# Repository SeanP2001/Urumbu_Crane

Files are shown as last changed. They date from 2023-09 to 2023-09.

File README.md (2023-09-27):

# Urumbu Crane

## Table of Contents <!-- omit from toc -->

- [Introduction](#introduction)
- [Design](#design)
  - [Y-Axis Drum](#y-axis-drum)
  - [X-Axis Drive Section](#x-axis-drive-section)
  - [X-Axis Carriage](#x-axis-carriage)
  - [Tail Pulley](#tail-pulley)
  - [Hook](#hook)
  - [End Plates](#end-plates)
  - [Frame](#frame)
- [Manufacturing](#manufacturing)
  - [3D Printing](#3d-printing)
  - [CNC Routing](#cnc-routing)
  - [Laser Cutting](#laser-cutting)
  - [Assembling](#assembling)
- [Software](#software)
- [Build Video and Demonstration](#build-video-and-demonstration)
- [Conclusion](#conclusion)

## Introduction

I designed a set of Urumbu USB stepper motor modules for students in the FabLAB to use for rapidly prototype motion systems. The files to create these modules can be found in my ["Urumbu_USB_Stepper_Motor" repostiory](https://github.com/SeanP2001/Urumbu_USB_Stepper_Motor). 

I designed and built this crane to test and demonstrate the use of the modules. This repository serves as documentation of a project which students can reference when learning how to use the modules.

## Design

<p align="center">
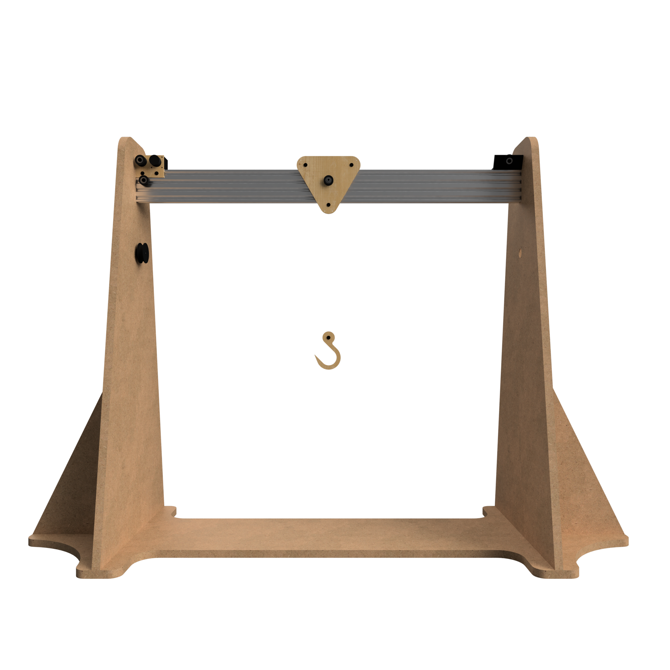
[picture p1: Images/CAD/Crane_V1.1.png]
  
</p>

### Y-Axis Drum

<p align="center">
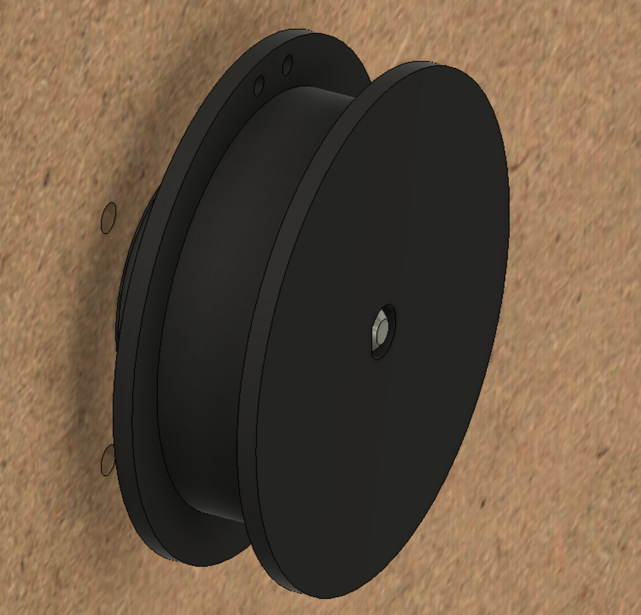
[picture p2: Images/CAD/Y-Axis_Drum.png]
   
</p>

Design Features:
- Two holes to tie the fishing line to.
- Reels in the fishing line.
- Friction fits onto NEMA 14 motor D-shaft.

### X-Axis Drive Section

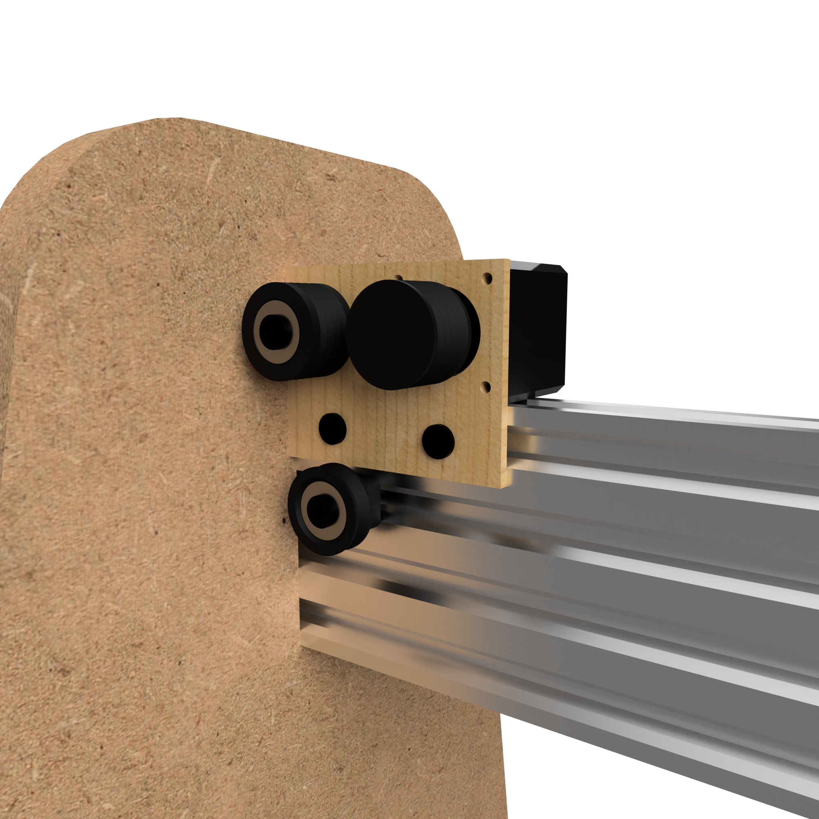
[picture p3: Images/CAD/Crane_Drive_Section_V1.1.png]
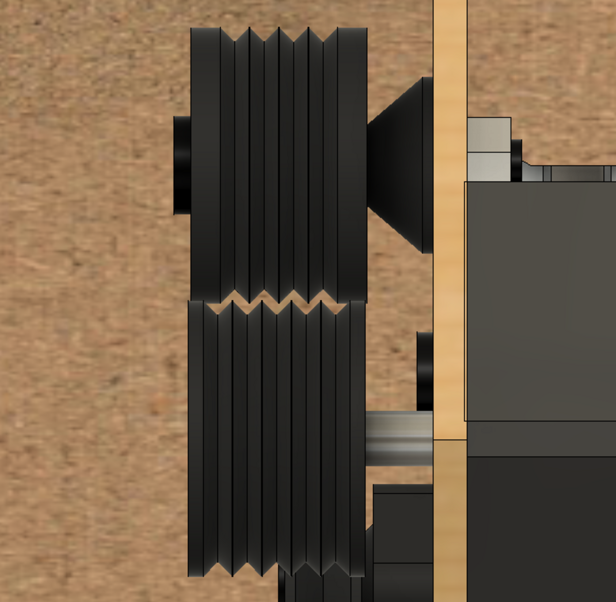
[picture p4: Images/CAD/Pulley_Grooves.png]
|   |  |
| --- | --- |

Design Features:
- Mounts the NEMA 14 motor to the aluminium extrusion.
- Secured to the aluminium extrusion using two M5 tee-nuts.
- Tensioner pulley increases friction between the motor pulley and fishing line, preventing it from slipping.
- Tensioner pulley has two bearings to help the fishing line move smoothly.

### X-Axis Carriage

<p align="center">
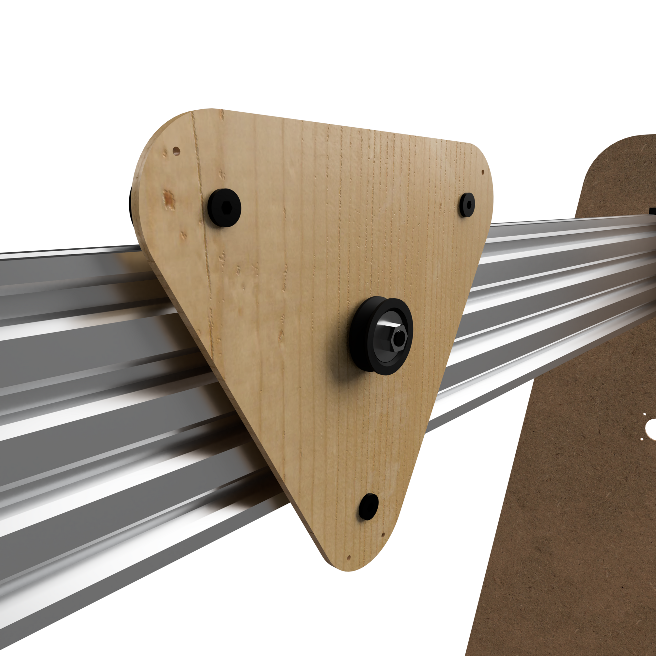
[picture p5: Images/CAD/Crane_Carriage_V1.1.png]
   
</p>

Design Features:
- Three M5 bolts secure spacers and Delrin V-wheels 
- The V-wheels slot into the V-slot linear rail, allowing the carriage to glide smoothly along the axis.
- Two holes for tying the x-axis fishing line to.
- A central pulley, to allow the fishing line to run over it and down to the hook.
- Two holes for the y-axis fishing line to be tied to after going through the hook. (There are two symmetrical holes to allow for the fishing line to come from the left or right side of the crane)

### Tail Pulley

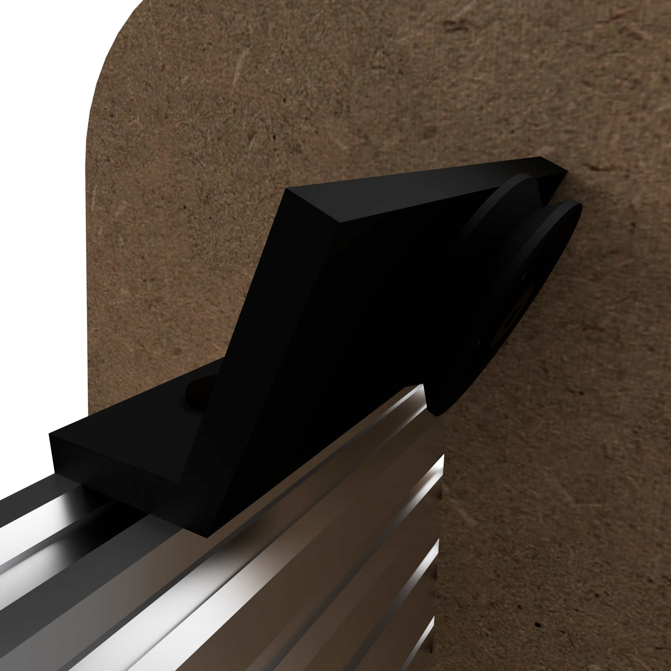
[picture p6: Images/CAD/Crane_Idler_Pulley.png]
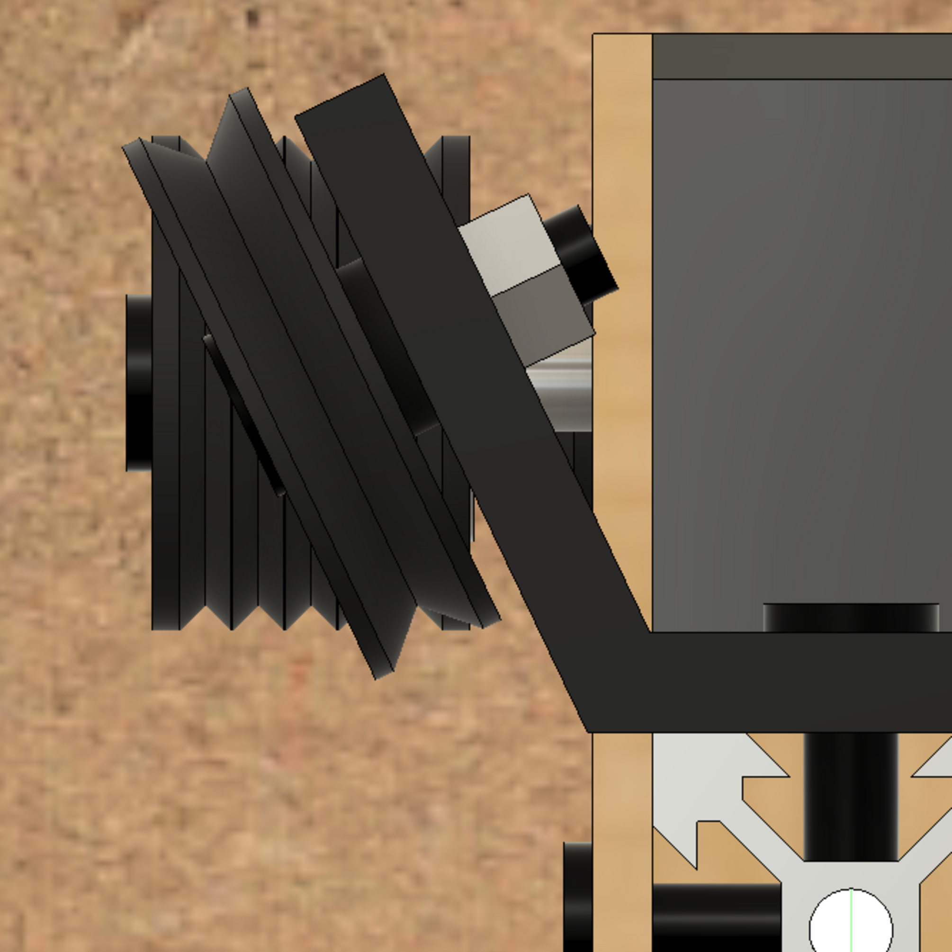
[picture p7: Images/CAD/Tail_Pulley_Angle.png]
|   |  |
| --- | --- |

Design Features:
- 3D printed bracket to secure the pulley to the aluminium extrusion at an angle. The angle matches the angle of the fishing line, allowing it to travel in a straight line from the motor pulley.
- Mounted to the extrusion with two M5 tee-nuts.

### Hook

<p align="center">
   
</p>

Design Features:
- Made from 5 layers of laser cut 3mm plywood glued together.
- Includes a pulley for the fishing line to go through and back up to the carriage. The doubled-up line prevents the hook from easily spinning.

### End Plates

<p align="center">
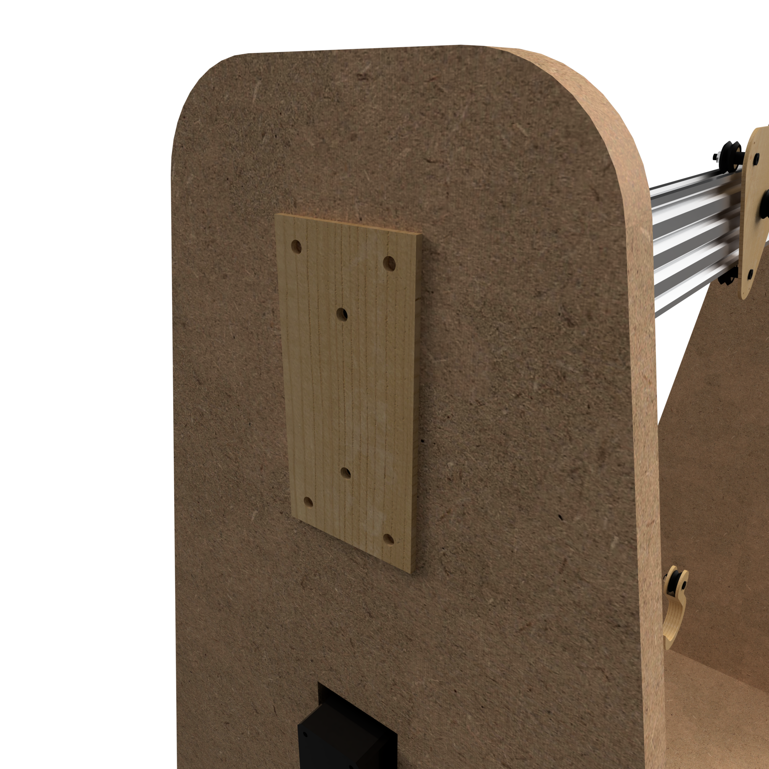
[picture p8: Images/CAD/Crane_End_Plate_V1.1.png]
   
</p>

Design Features:
- Two central holes to secure the plates to the tapped holes in the aluminium extrusion using M5 bolts.
- Four corner holes to secure the plates to the MDF frame with self-tapping wood screws.  

### Frame

<p align="center">
   
</p>

Design Features:
- Slot together with mortise and temon joints (dogboned to take into account the radius of the end mill)
- Symmetrical to allow the Y-axis motor to be mounted on either the left or right side.

## Manufacturing

### 3D Printing

I created a new Fusion360 file and imported the 3D printed bodies from the main Fusion360 file. I then laid out all of the parts flat on the XZ plane before exporting the STL file.

I opened the STL file in Cura and sliced the file for my 3D printer. I saved the Gcode to the microSD card to transfer the file to the printer.

<p align="center">
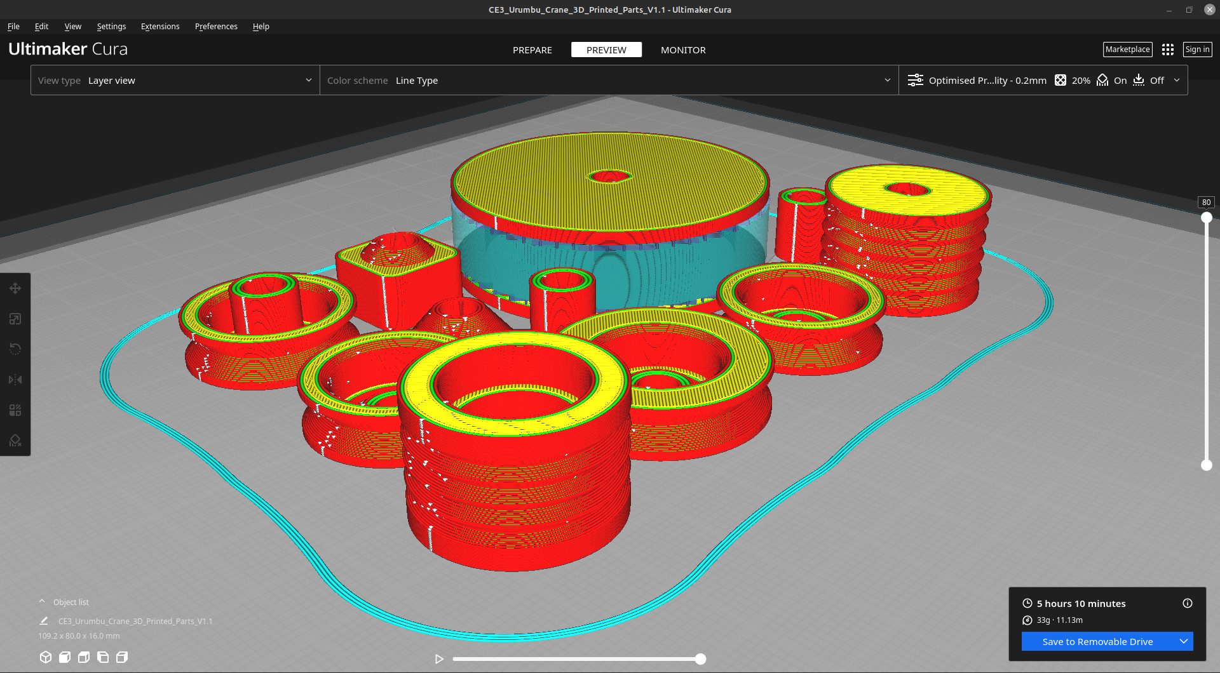
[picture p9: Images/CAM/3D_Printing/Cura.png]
  
</p>

I printed the parts using black PLA filament.

<p align="center">
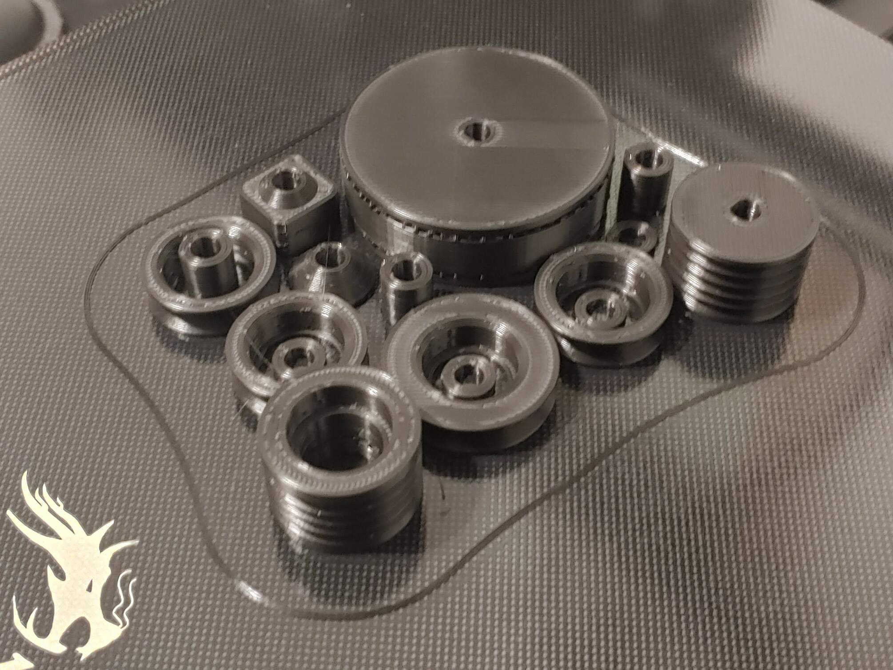
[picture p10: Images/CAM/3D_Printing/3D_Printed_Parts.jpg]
  
</p>

### CNC Routing

The MDF parts were imported into two new Fusion 360 designs, laid flat on the XZ plane and arranged to fit 8’x4’ sheets of MDF. Using the "Manufacturing" workspace, a new "Setup" was created, defining the type of CNC operation and the material properties. The "2D Pocket" and "2D Contour" operations were used to create the toolpaths.

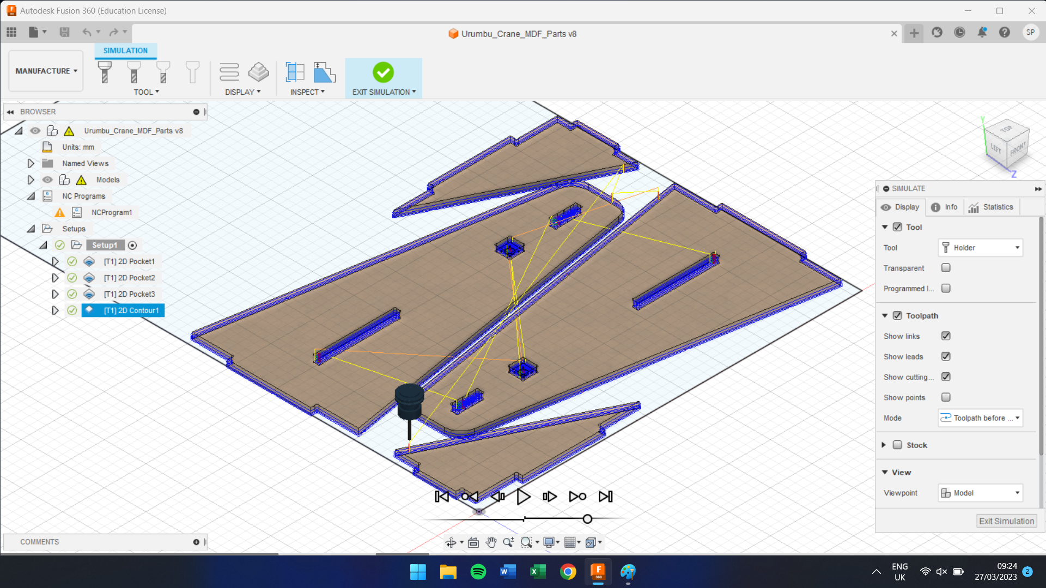
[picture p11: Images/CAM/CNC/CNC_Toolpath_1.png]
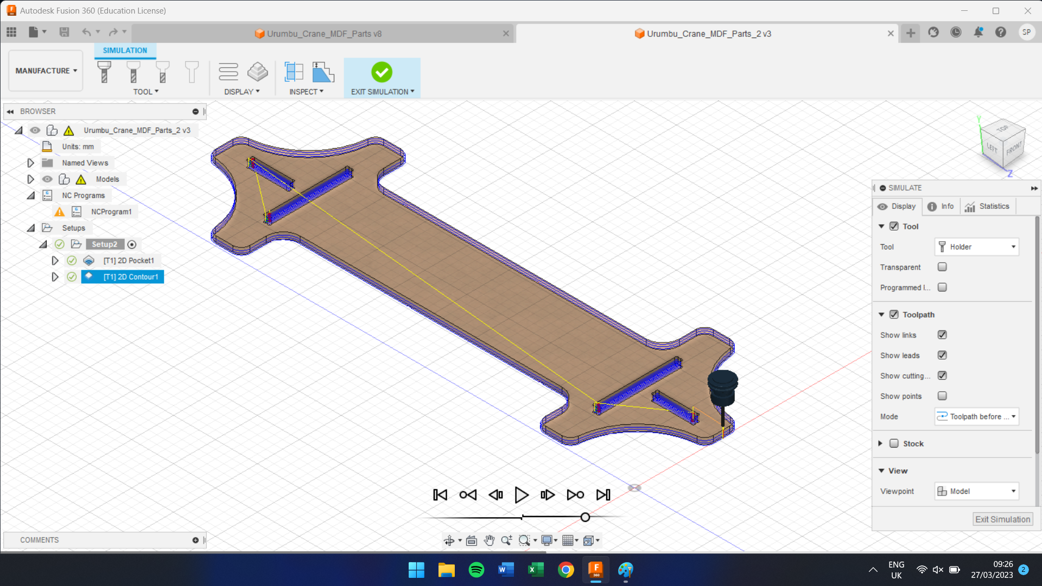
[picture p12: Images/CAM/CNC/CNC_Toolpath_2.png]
|   |  |
| --- | --- |

The toolpaths were exported as `.nc` files and saved to a USB stick. The USB stick was plugged into the large format CNC machine controller. The MDF was placed on the CNC, the vacuum table and extraction were turned on, the origins were set and the files were selected to cut.

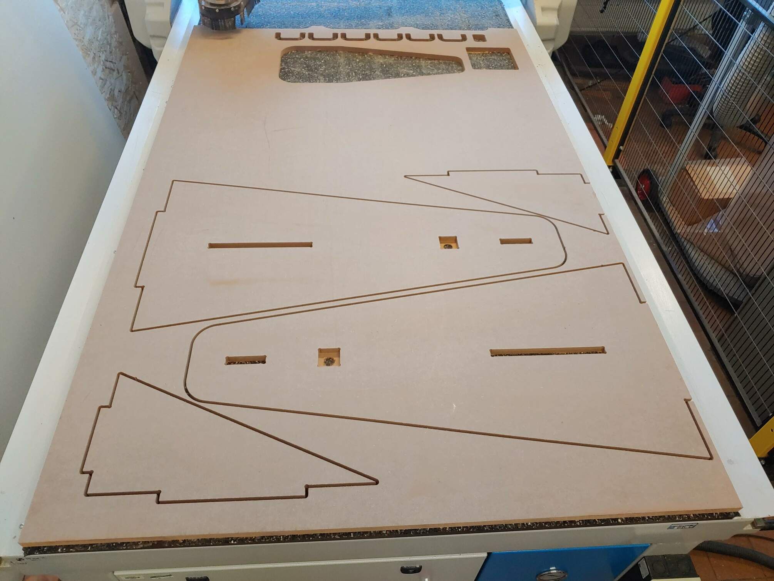
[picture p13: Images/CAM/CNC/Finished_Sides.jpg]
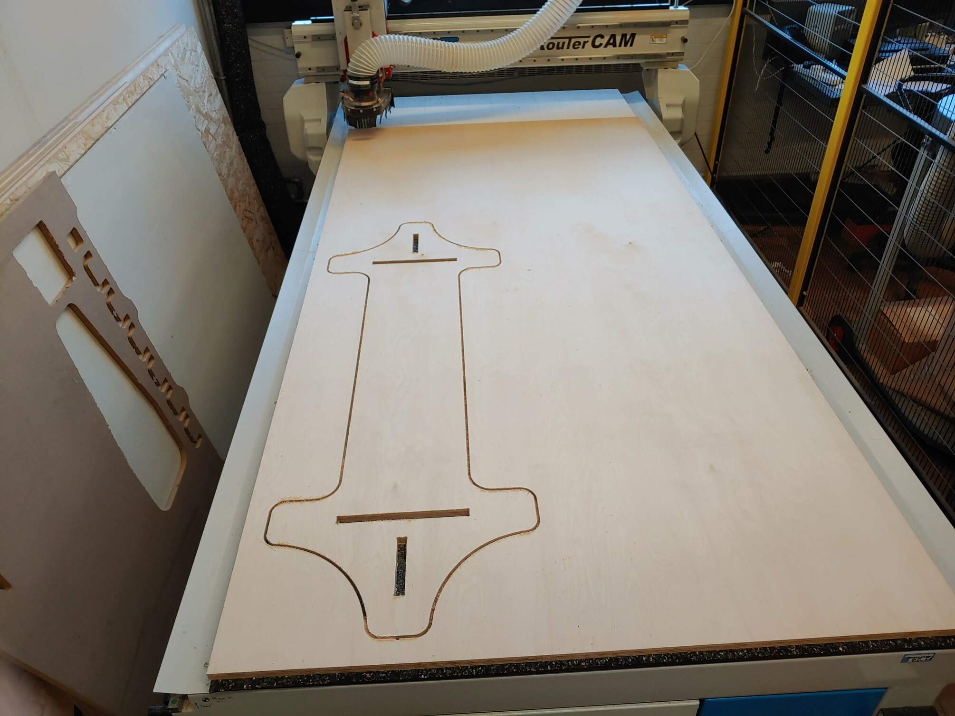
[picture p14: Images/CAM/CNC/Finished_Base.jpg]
|   |  |
| --- | --- |

### Laser Cutting

Using the Fusion 360 app "Shaper", I created SVG images for all the profiles that needed laser cutting.

<p align="center">
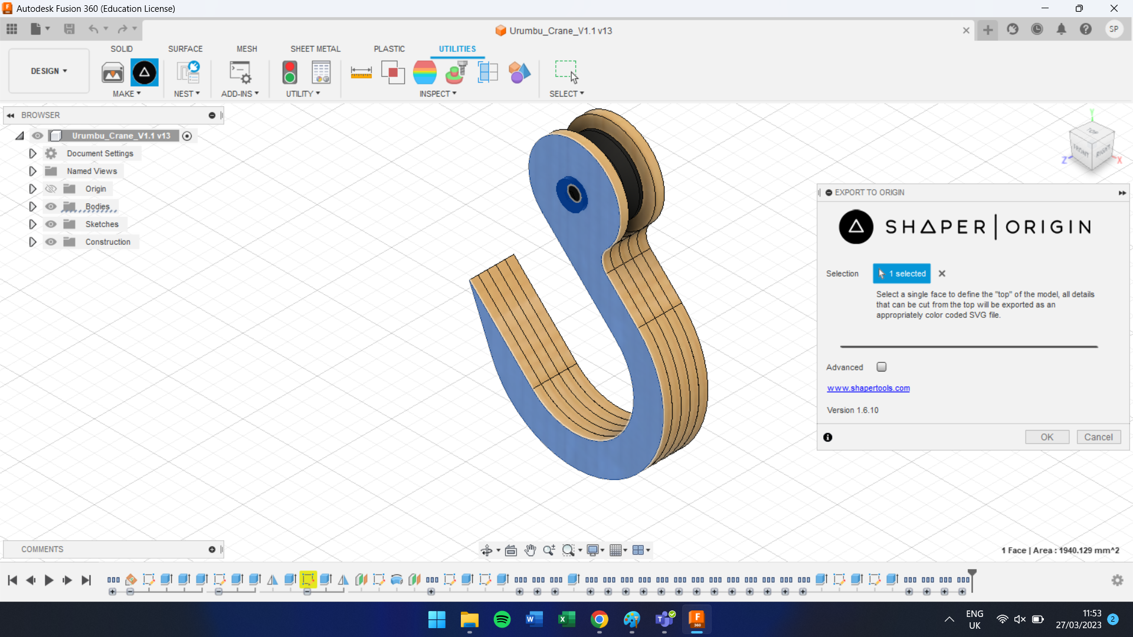
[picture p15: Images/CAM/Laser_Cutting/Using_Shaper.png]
  
</p>

This created SVG images of the end plate, carriage, outer hook, inner hook and motor mount profiles.

These profiles were imported into Inkscape and altered to have a red outline with no fill. The profiles were arranged to best use the space.

<p align="center">
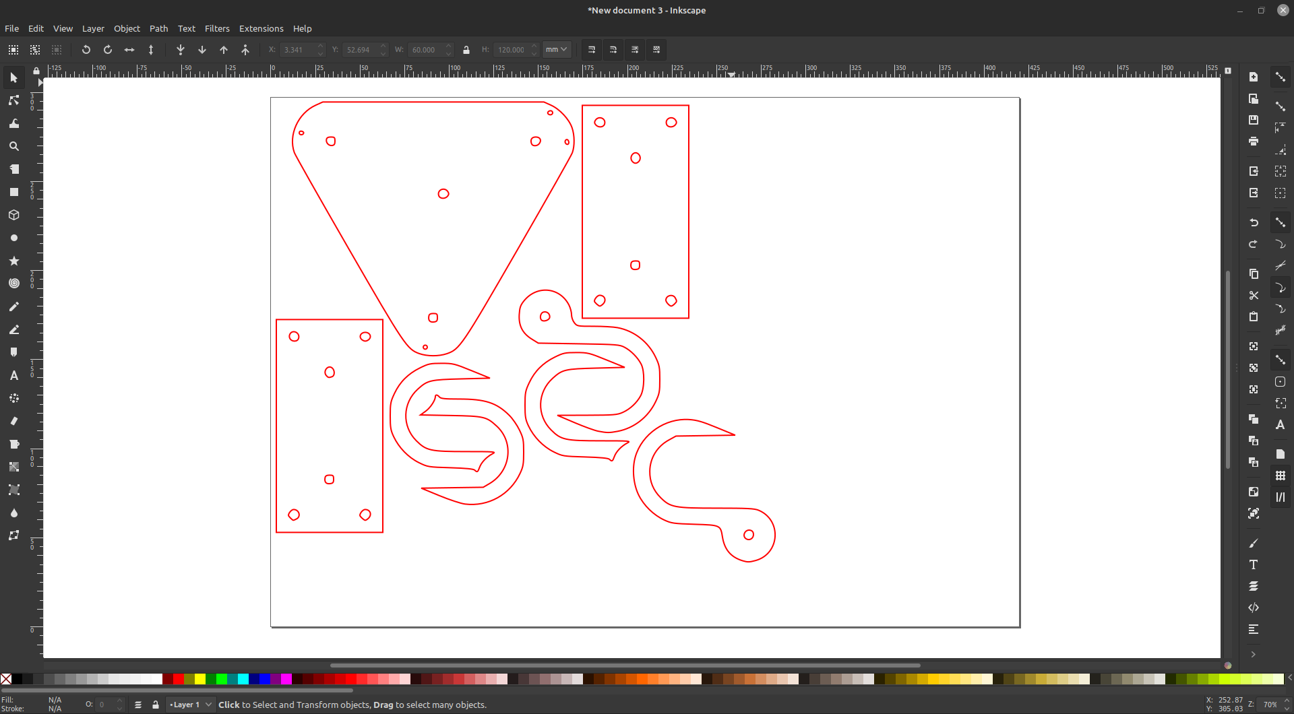
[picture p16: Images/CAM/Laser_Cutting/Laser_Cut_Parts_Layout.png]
  
</p>

In CorelDRAW, all lines were set to hairline thickness, and the file was sent to "print" on the Trotec Speedy400 laser-cutter. This opened Trotec JobControl. 

The 3mm Plywood was placed on the bed of the laser cutter, the laser height and position were set, and the lid was closed. In JobControl, the file was dragged to the position of the laser and set to cut.

<p align="center">
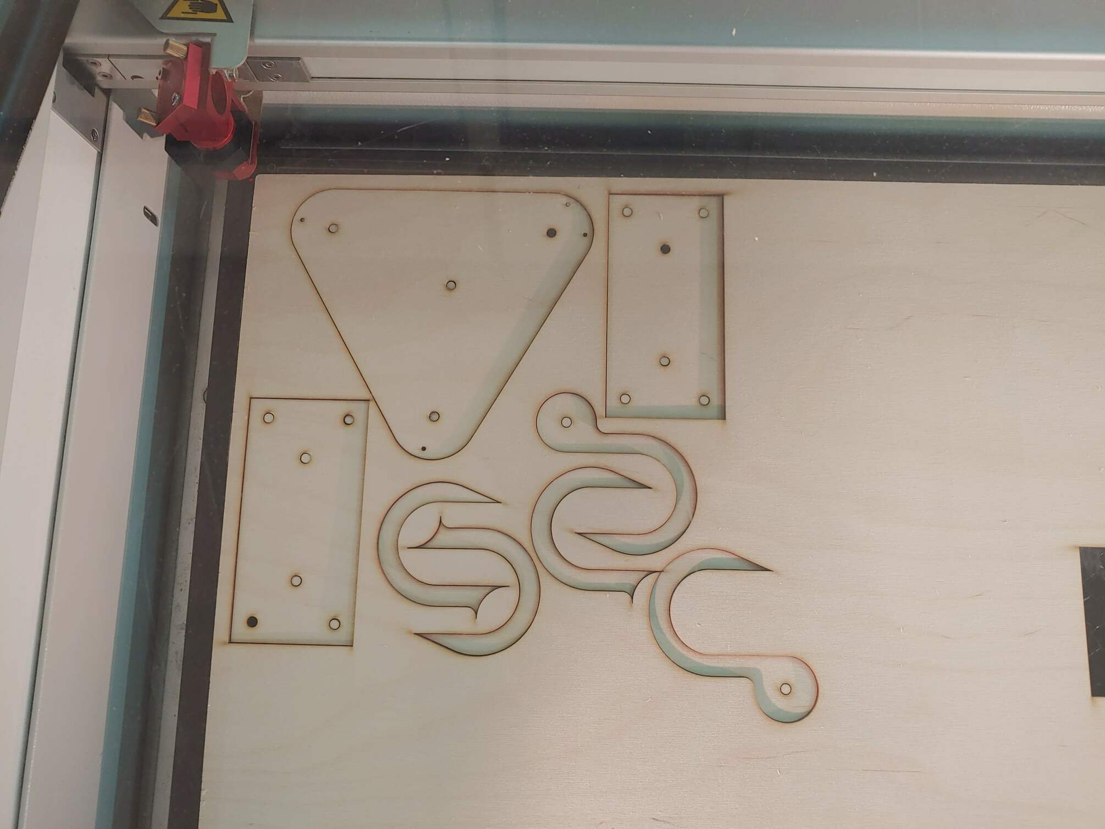
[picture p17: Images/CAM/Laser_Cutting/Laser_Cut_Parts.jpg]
  
</p>

### Assembling

- Slotted the frame together.
- Tapped M5 threads into 80x20x1000mm aluminium extrusion ends.
- Bolted the end plates to the ends of the aluminium extrusion.
- Screwed the end plates to the frame.

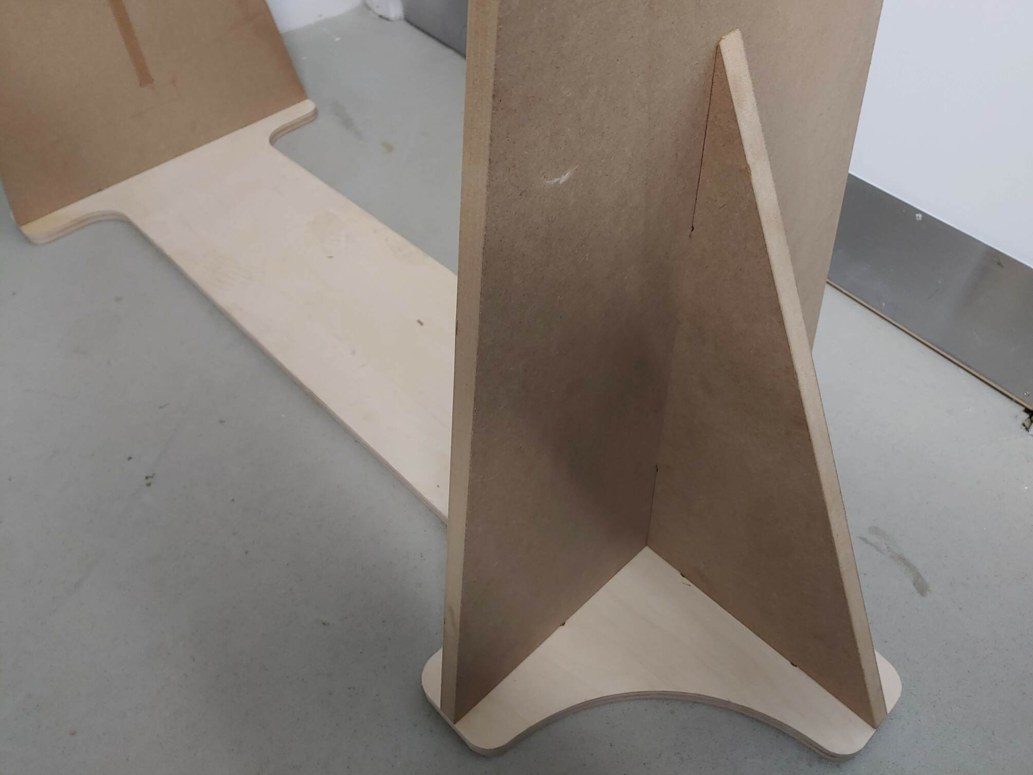
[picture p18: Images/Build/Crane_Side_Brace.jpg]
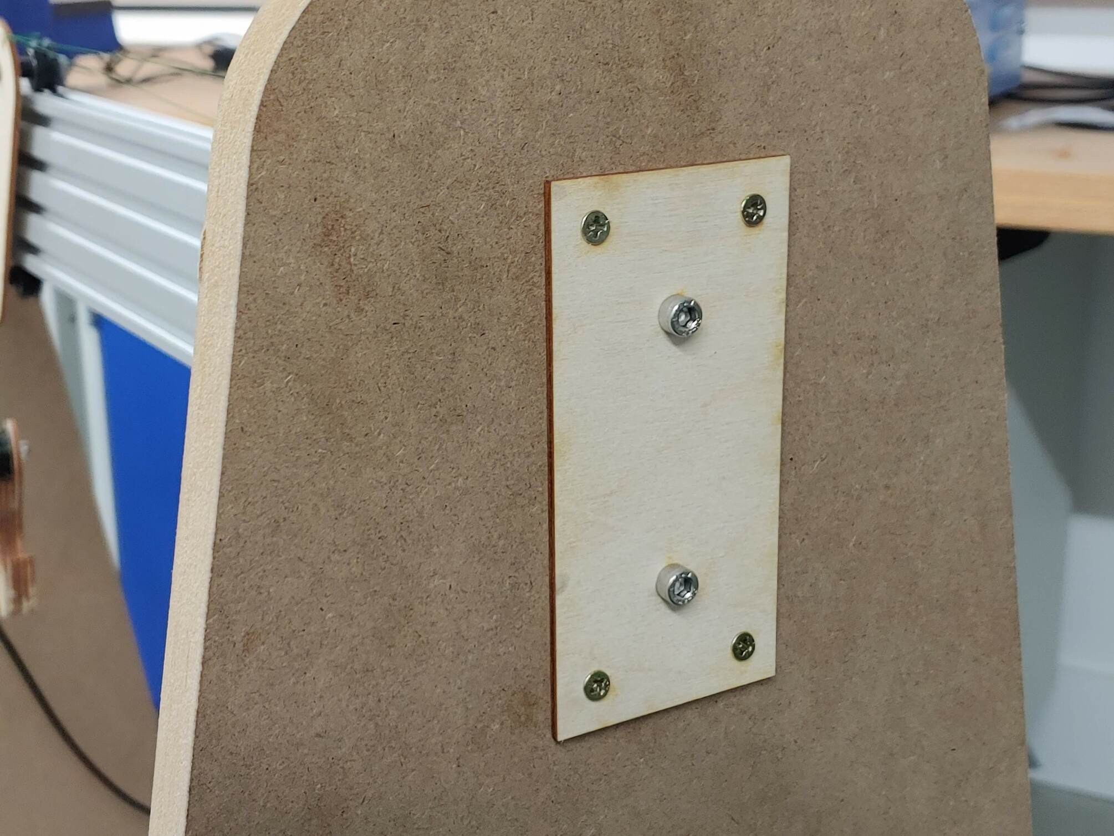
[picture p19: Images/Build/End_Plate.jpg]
|   |  |
| --- | --- |
  
- Glued the hook profiles together.
  
<p align="center">
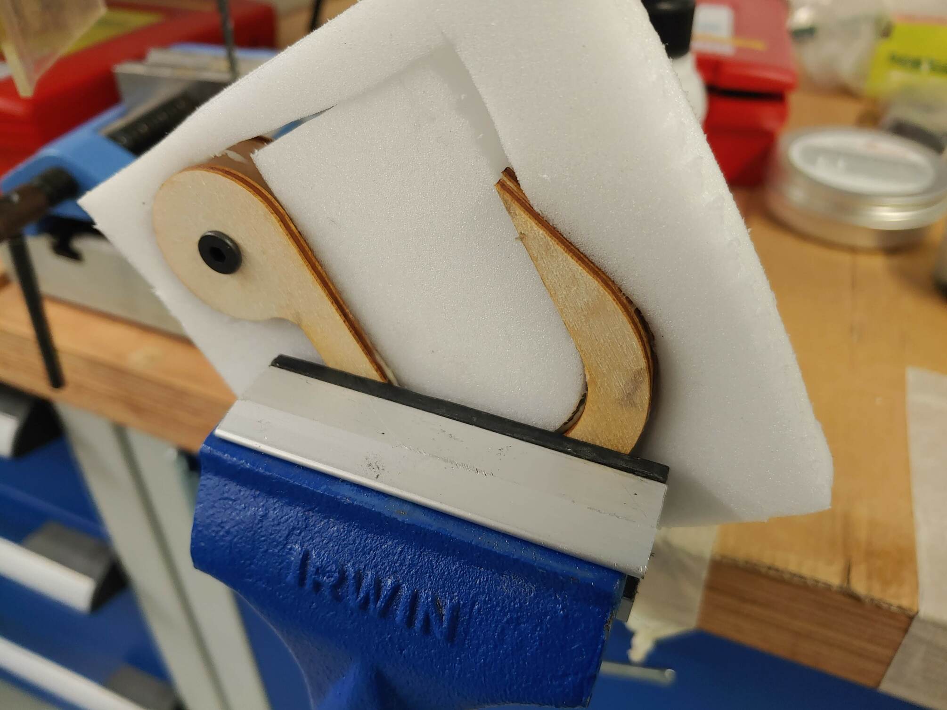
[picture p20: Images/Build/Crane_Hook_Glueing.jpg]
  
</p>

- Fixed both motors in place using M3 bolts.
- Covered the backs of both motors with electrical tape to prevent short circuits.
- Bolted Urumbu modules to the back of the motors using M3 bolts and several nylon washers.
- Plugged the stepper motor cables into the headers on the Urumbu boards.

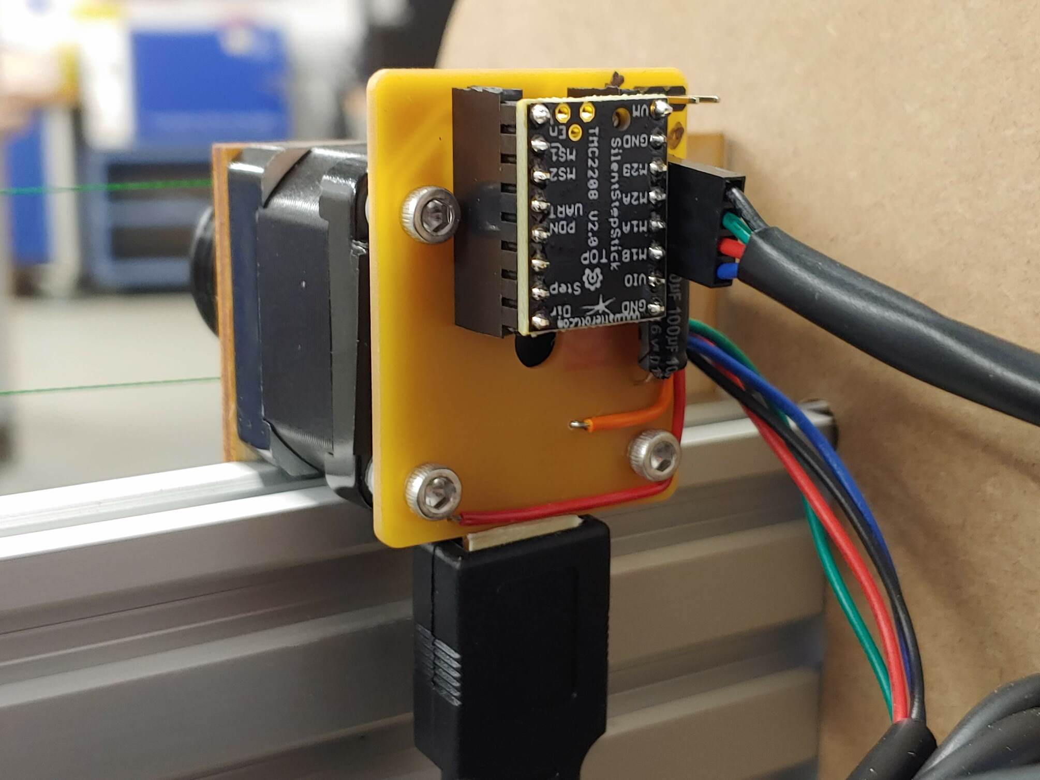
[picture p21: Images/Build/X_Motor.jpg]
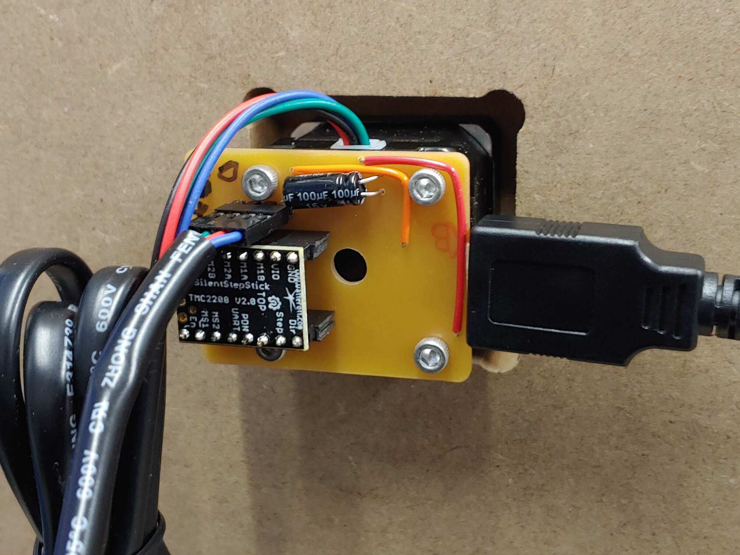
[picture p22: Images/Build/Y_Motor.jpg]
|   |  |
| --- | --- |

- Press fitted the X-axis motor pulley and Y-axis drums onto the motor shafts.
- Secured the X-axis motor mount, tail pulley bracket and other parts to the aluminium extrusion using M5 bolts and tee-nuts.

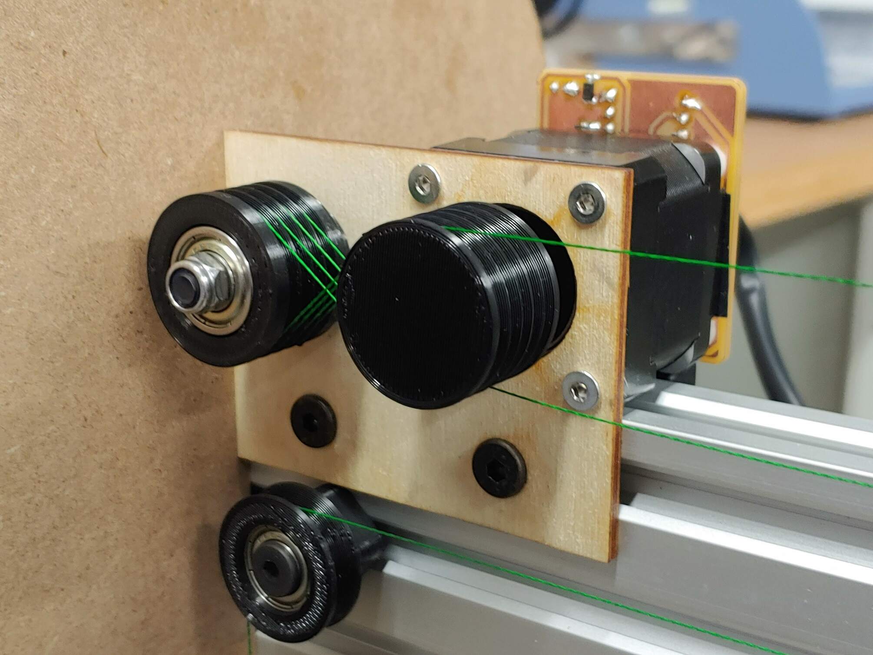
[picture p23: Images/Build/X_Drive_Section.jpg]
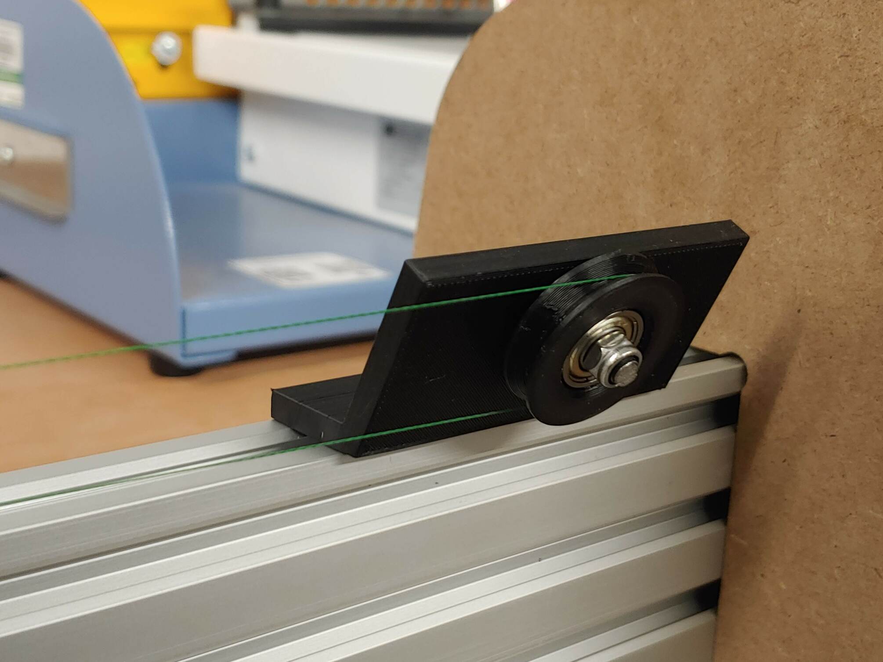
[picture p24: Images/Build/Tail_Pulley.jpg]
|   |  |
| --- | --- |

- Secured the carriage pulley to the carriage using a spacer with an M5 nut and bolt.
- Bolted the top two Delrin V-wheels to the carriage with spacers along with M5 nuts and bolts.
- Placed the carriage on the extrusion with the top V-wheels slotted into the top V-slot.
- Held the third V-wheel in place underneath the extrusion and secured it to the carriage.

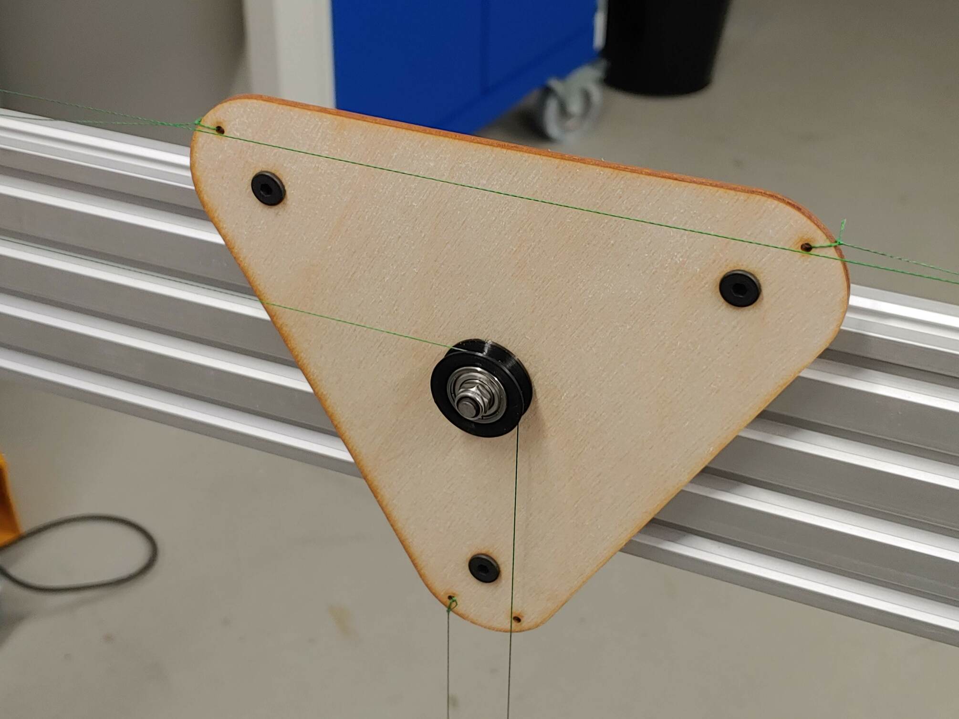
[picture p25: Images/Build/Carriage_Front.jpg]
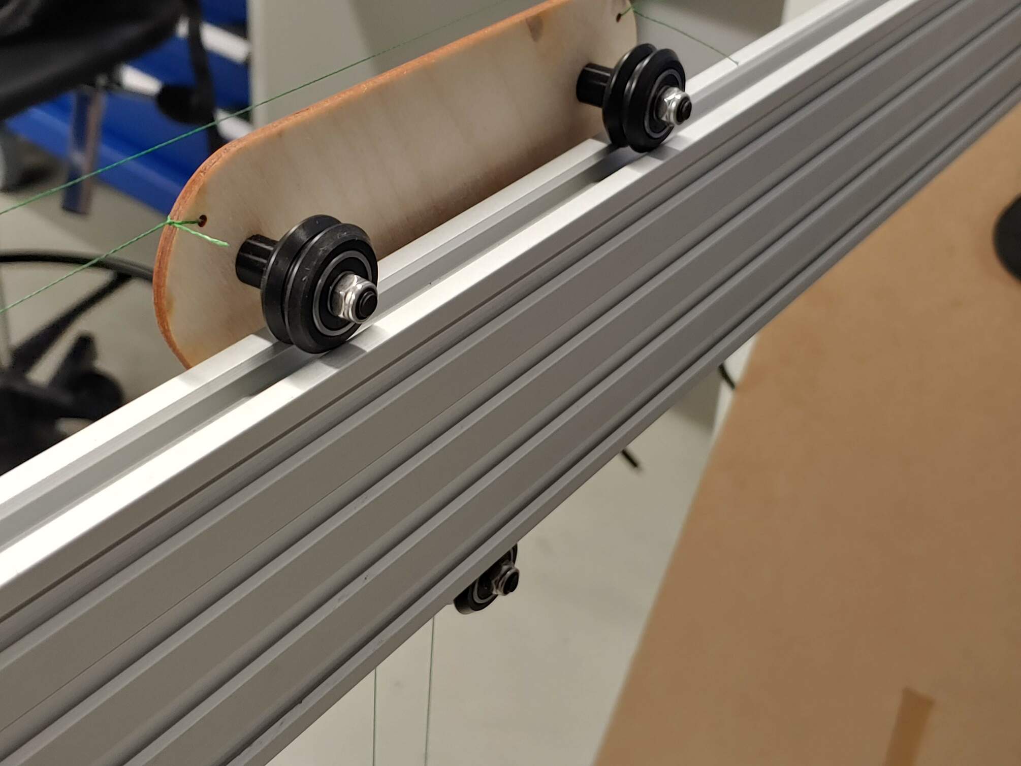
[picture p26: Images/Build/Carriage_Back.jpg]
|   |  |
| --- | --- |

- Tied the fishing line to one side of the carriage.
- Wrapped the line around the X-axis motor pulley and tensioner pulley in a figure-eight.
- Looped the line around the tail pulley.
- Tied the line to the other side of the carriage.

<p align="center">
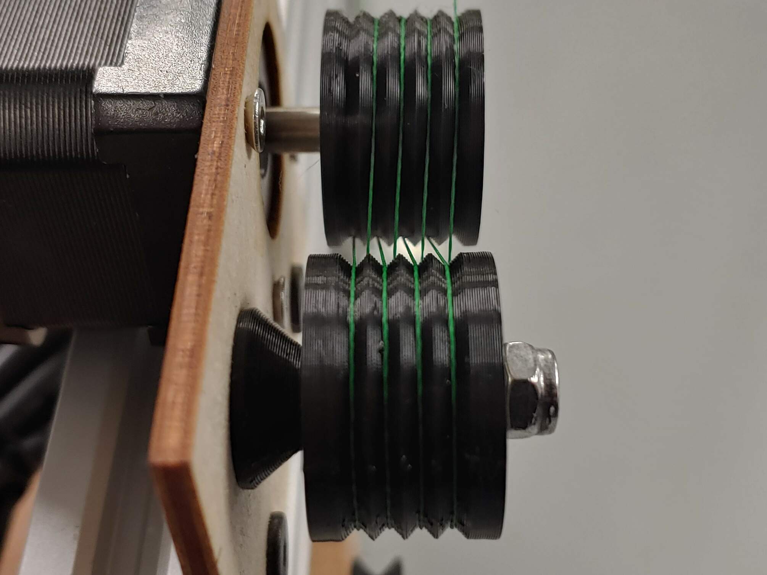
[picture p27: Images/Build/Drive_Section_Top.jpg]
  
</p>

- Tied a second piece of fishing line to the bottom of the carriage.
- Threaded the line through the hook pulley, over the carriage pulley and the second pulley.
- Tied the line to the Y-axis drum with enough slack for the hook to touch the floor at the far end of the X-axis travel.
- Wound the line up on the Y-axis drum.

<p align="center">
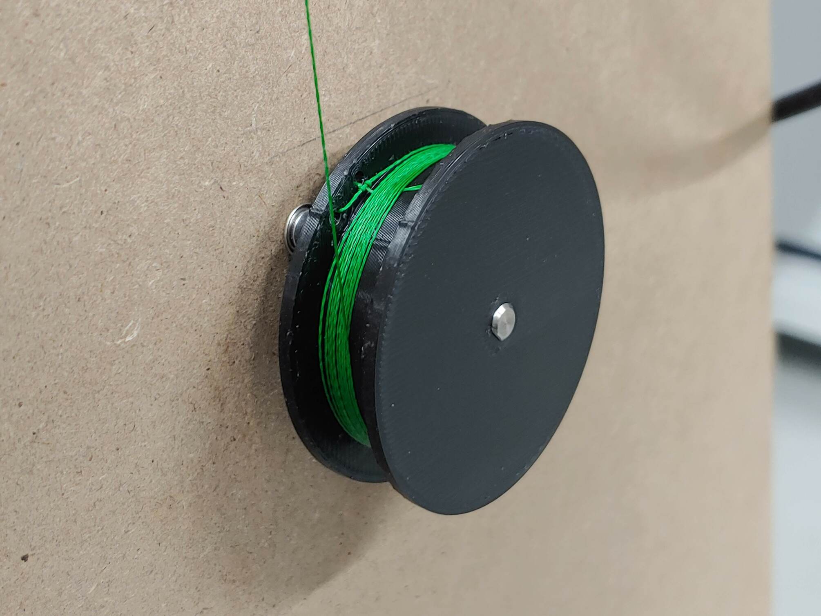
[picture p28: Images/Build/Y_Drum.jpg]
  
</p>

The complete crane was assembled in less than three hours.

<p align="center">
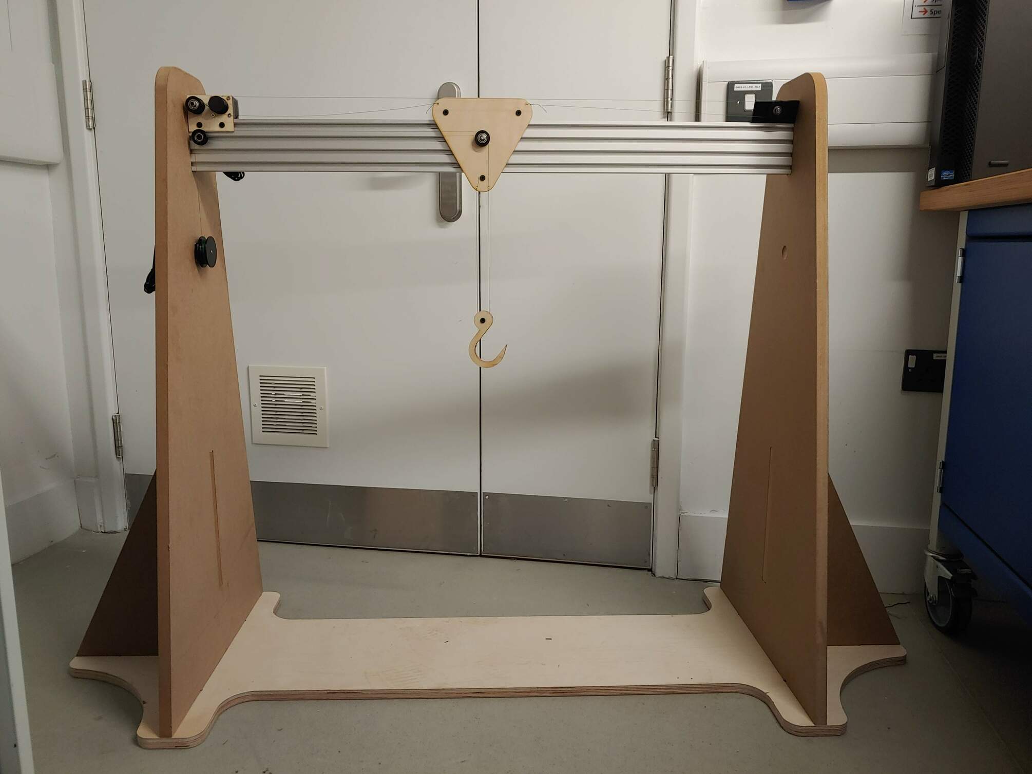
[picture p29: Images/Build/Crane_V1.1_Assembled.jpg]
  
</p>

## Software

I programmed a graphical controller program in Python using the PySimpleGUI library. The graphical interface allows users to select the USB port for each motor and connect to them. They can set upper and lower limits for each axis, change the movement speed and control the crane.

<p align="center">
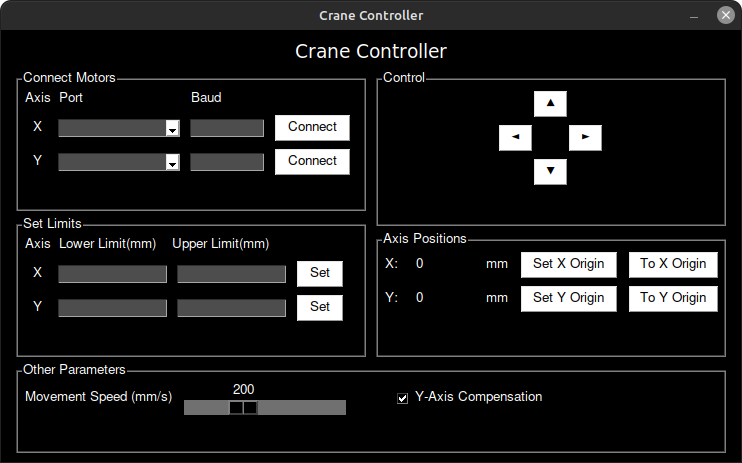
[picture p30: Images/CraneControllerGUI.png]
  
</p>

## Build Video and Demonstration

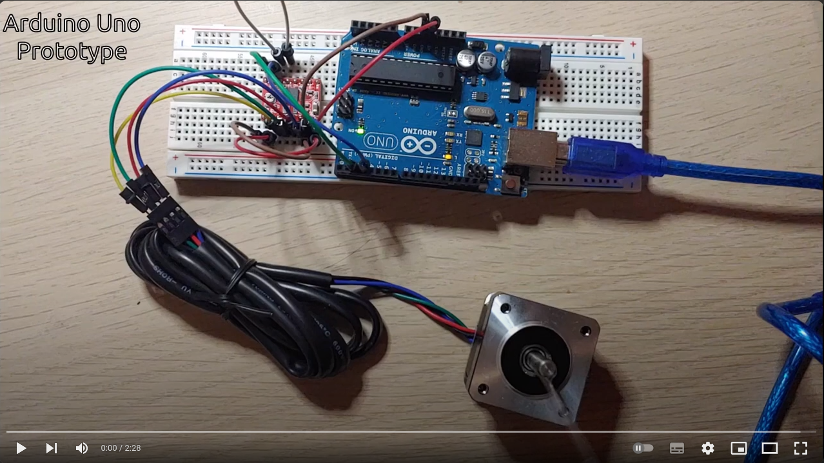
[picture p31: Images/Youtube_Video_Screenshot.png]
[](https://www.youtube.com/watch?v=1Sd0MmUDr9s&ab_channel=SeanPrice)

## Conclusion

The modules were quick and easy to use to prototype a working motion system. They were reliable, which made troubleshooting my code much easier. One area of improvement is that inefficiencies in the code caused the crane to move slowly at times. Using multiple CPU cores would allow multiple sections of code to run simultaneously, allowing the crane to run at full speed.

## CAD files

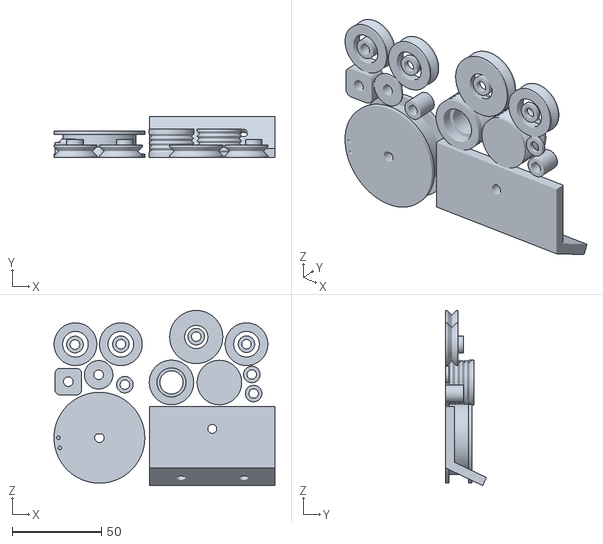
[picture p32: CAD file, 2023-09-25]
CAD/Urumbu_Crane_3D_Printed_Parts_V1.1.stl
124.0 x 23.0 x 98.3

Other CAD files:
CAD/Urumbu_Crane_MDF_Parts.f3z
CAD/Urumbu_Crane_MDF_Parts_2.f3z
CAD/Urumbu_Crane_V1.1.f3d

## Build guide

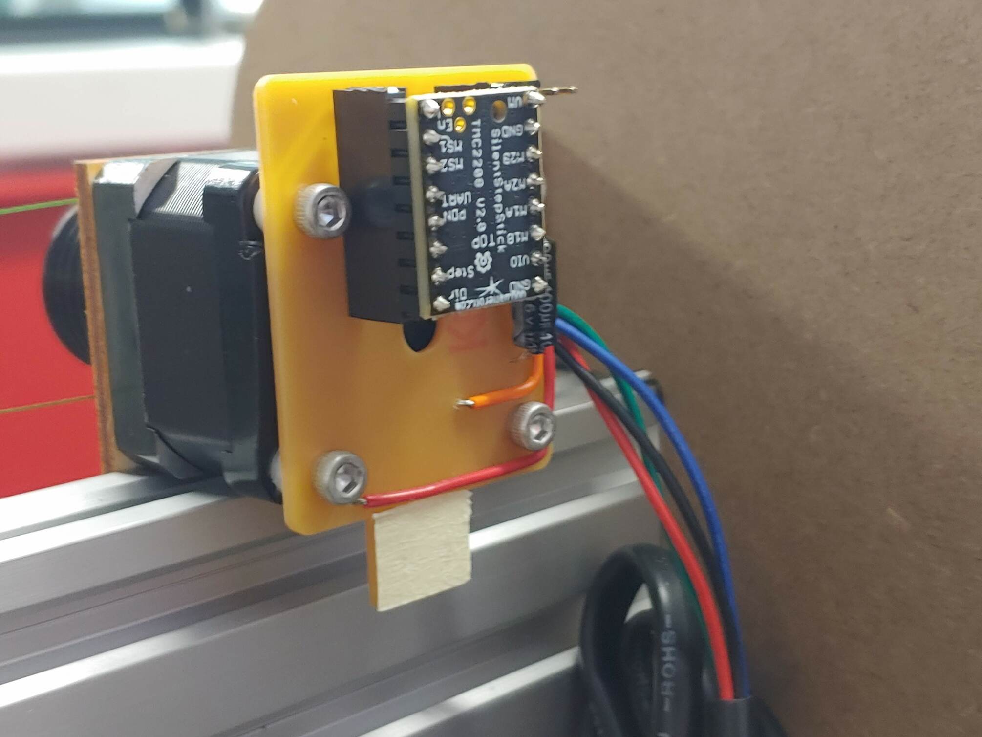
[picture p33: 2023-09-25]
Images/Build/20230207_094220.jpg

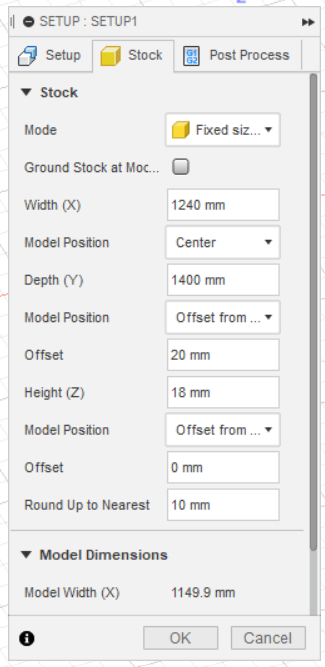
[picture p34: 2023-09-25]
Images/CAM/CNC/CNC_CAM_Material_Setup.png

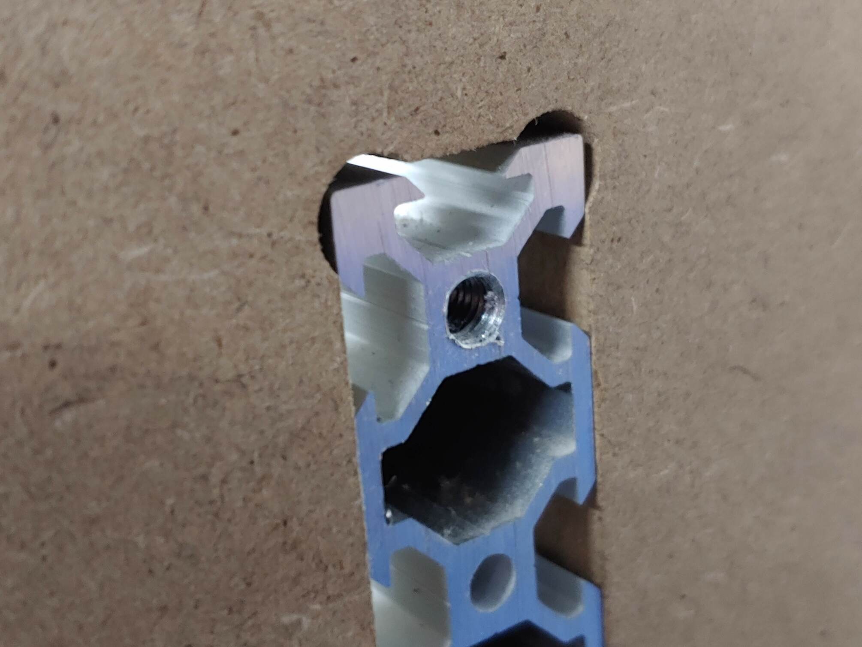
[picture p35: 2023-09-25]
Images/Build/Tapped_Aluminium_Extrusion.jpg

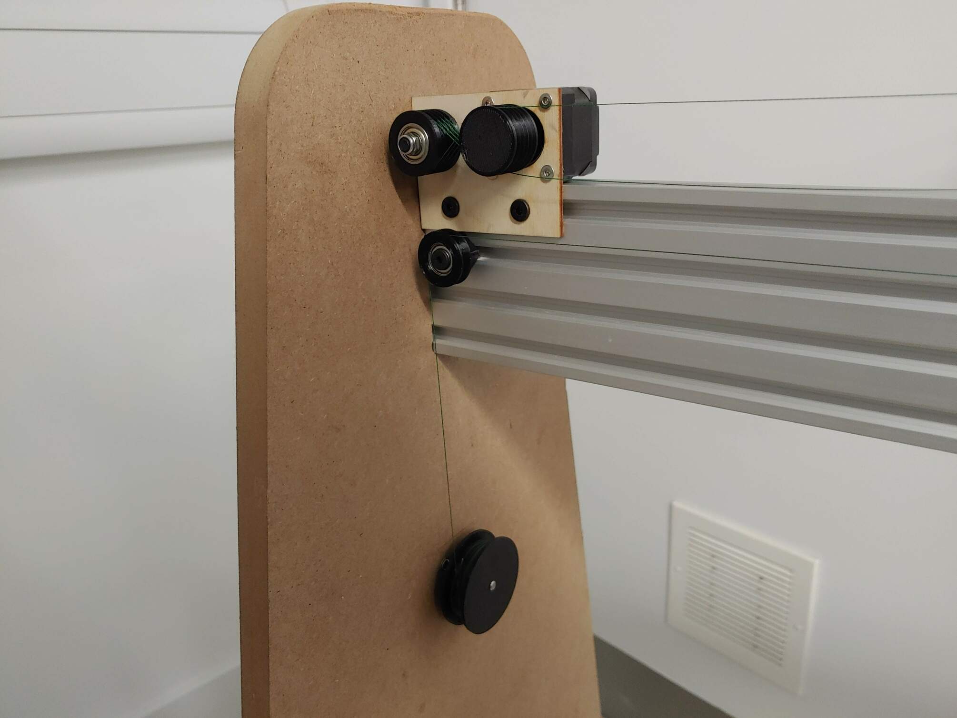
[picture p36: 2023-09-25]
Images/Build/Crane_V1.1_Pullys.jpg

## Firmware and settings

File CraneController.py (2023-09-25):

import serial,sys,time,signal,keyboard
import PySimpleGUI as sg
import serial.tools.list_ports
import math
import random

forward = b'f'                                                # send 'f' to drive the motor forward/clockwise
reverse = b'r'                                                # send 'r' to drive the motor reverse/anti-clockwise

#------------------------------------------------------------------------------- A X I S -------------------------------------------------------------------------------  
class Axis:
    def __init__(self, pulleyDiameter, degreesPerStep, microsteps, position, lowerLimit, upperLimit, mmPerSec, doubled=False):
        self.pulleyDiameter = pulleyDiameter
        self.degreesPerStep = degreesPerStep
        self.microsteps = microsteps
        self.position = position
        self.lowerLimit = lowerLimit
        self.upperLimit = upperLimit
        self.mmPerSec = mmPerSec
        self.doubled = doubled
        
        self.calcStepsPerRev()
        self.calcMmPerStep()
        self.calcStepDelay()

    def calcStepsPerRev(self):
        degPerMicrostep = self.degreesPerStep / self.microsteps        
        self.stepsPerRevolution = 360 / degPerMicrostep
        
    def calcMmPerStep(self):
        pulleyCircumference = math.pi * self.pulleyDiameter
        self.mmPerStep = pulleyCircumference / self.stepsPerRevolution
        
        if self.doubled == True:
            self.mmPerStep = self.mmPerStep / 2
        
    def calcStepDelay(self):
        stepsPerSec = self.mmPerSec / self.mmPerStep
        self.stepDelay = 1 / stepsPerSec
        
    def connectMotor(self, port, baud):
        self.motor = serial.Serial(port, baud, timeout=0)     # connect to the specified serial port at the specified baud rate
        
    def setLimits(self, lowerLimit, upperLimit):
        self.lowerLimit = lowerLimit
        self.upperLimit = upperLimit
    
    def setPulleyDiameter(self, mmDiameter):
        self.pulleyDiameter = mmDiameter
        self.calcMmPerStep()
        self.calcStepDelay()
        
    def setSpeed(self, mmPerSec):
        self.mmPerSec = mmPerSec
        self.calcStepDelay()
    
    def setOrigin(self):
        self.position = 0                                     # Set the current axis position to 0
    
    def stepClockwise(self):
        self.motor.write(forward)                             # send an 'f' to the motor to rotate 1 step clockwise  
        self.position = self.position - self.mmPerStep        # decrease the position by 1 step (in mm)
    
    def stepAntiClockwise(self):
        self.motor.write(reverse)                             # send an 'r' to the motor to rotate 1 step anti-clockwise
        self.position = self.position + self.mmPerStep        # increase the position by 1 step (in mm)
    
    def adjustClockwise(self):
        self.motor.write(forward)                             # send an 'f' to the motor to rotate 1 step clockwise  
    
    def adjustAntiClockwise(self):
        self.motor.write(reverse)                             # send an 'r' to the motor to rotate 1 step anti-clockwise
        
    def isWithinLimit(self, end):
        if end == "lower":
            return self.position > self.lowerLimit
        elif end == "upper":
            return self.position < self.upperLimit 

x = Axis(23.05, 1.8, 8, 0, 0, 610, 200)                                # Axis (pulleyDiameter, degreesPerStep, microsteps, position, lowerLimit, upperLimit, mmPerSec, doubled=False)
y = Axis(40.85, 1.8, 8, 0, -698, 0, 200, doubled=True)


#---------------------------------------------------------------- Y   A X I S   C O M P E N S A T I O N ---------------------------------------------------------------- 
def calcYCompStepsPerXStep(x, y, yMovesBy, overXDist):
    yAxisMovement = yMovesBy / overXDist
    xStepsPerMm = 1 / x.mmPerStep
    yStepsPerMm = 1 / y.mmPerStep
    return ( yStepsPerMm * yAxisMovement ) / xStepsPerMm
        
overXDist = 625                                                        # When moving the crane this far (mm) in the x axis (without Y comp enabled)
yMovesBy = 309.5                                                       # The y axis moves by this distance (mm) 

yCompStepsPerXStep = calcYCompStepsPerXStep(x, y, yMovesBy, overXDist) # calculate how many steps the Y axis has to move for each X axis step to compensate and stay at the same height

yCompEnabled = True                                                    # enable Y axis compensation by default


#---------------------------------------------------------------------- W I N D O W   L A Y O U T ---------------------------------------------------------------------- 
minSpeed = 50                                                 # Minimum movement speed in mm/s
maxSpeed = 500                                                # Maximum movement speed in mm/s

ports = serial.tools.list_ports.comports()                    # get a list of all of the COM ports

sg.theme('Black')                                             # Set the colour theme for the application

connectMotors = [
    sg.Frame("Connect Motors",
    [
        [
            sg.Text("Axis  Port                           Baud")
        ],
        [
            sg.Text("  X "), 
            sg.Combo([port for port in sorted(ports)], s=(15,30), enable_events=True, readonly=True, key='-X_PORT-'),
            sg.Input(key='-X_BAUD-', s=(10,1)),
            sg.Button('Connect', key="-CONNECT_X-")
        ],
        [
            sg.Text("  Y "), 
            sg.Combo([port for port in sorted(ports)], s=(15,30), enable_events=True, readonly=True, key='-Y_PORT-'),
            sg.Input(key='-Y_BAUD-', s=(10,1)),
            sg.Button('Connect', key="-CONNECT_Y-")
        ]
    ], size=(350,140))
]

setLimits = [
    sg.Frame("Set Limits",
    [
        [
            sg.Text("Axis  Lower Limit(mm)    Upper Limit(mm)")
        ],
        [
            sg.Text("  X "), 
            sg.Input(key='-X_LOW_LIM-', s=(15,1), do_not_clear=False),
            sg.Input(key='-X_UP_LIM-', s=(15,1), do_not_clear=False),
            sg.Button('Set', key="-SET_X_LIM-")
        ],
        [
            sg.Text("  Y "), 
            sg.Input(key='-Y_LOW_LIM-', s=(15,1), do_not_clear=False),
            sg.Input(key='-Y_UP_LIM-', s=(15,1), do_not_clear=False),
            sg.Button('Set', key="-SET_Y_LIM-")
        ]
    ], size=(350,140))
]

dPad = [
    sg.Frame("Control",
    [
        [
            sg.RealtimeButton(sg.SYMBOL_UP, key='-UP-', size=(1,1))
        ],
        [
            sg.RealtimeButton(sg.SYMBOL_LEFT, key='-LEFT-', size=(1,1)),
            sg.Text(size=(3,1), justification='c', pad=(0,0)),
            sg.RealtimeButton(sg.SYMBOL_RIGHT, key='-RIGHT-', size=(1,1))
        ],
        [
            sg.RealtimeButton(sg.SYMBOL_DOWN, key='-DOWN-', size=(1,1))
        ]
    ], element_justification="c", size=(350,155))       
]

positions = [
    sg.Frame("Axis Positions", 
    [
        [
            sg.Text("X: "), sg.Text(x.position, s=(8,1), key="-X-"), sg.Text("mm"),
            sg.Button("Set X Origin", key='-SET_X_ORIG-', size=(10,1)),
            sg.Button("To X Origin", key='-TO_X_ORIG-', size=(10,1))
        ],
        [
            sg.Text("Y: "), sg.Text(y.position, s=(8,1), key="-Y-"), sg.Text("mm"),
            sg.Button("Set Y Origin", key='-SET_Y_ORIG-', size=(10,1)),
            sg.Button("To Y Origin", key='-TO_Y_ORIG-', size=(10,1))
        ]
    ], size=(350,125))
]

otherParameters = [
    sg.Frame("Other Parameters", 
    [
        [
            sg.Text("Movement Speed (mm/s)"),
            sg.Slider((minSpeed,maxSpeed), orientation='h', s=(18,15), key="-SPEED-", default_value=200, enable_events=True), 
            sg.Text("     "), 
            sg.Checkbox(' Y-Axis Compensation', key="-Y_COMP-", default=True, enable_events=True),
        ]
    ], size=(710,90))
]

layout = [
    [sg.T('Crane Controller', font='_ 14', justification='c', expand_x=True)],
    [
        sg.Col(
        [
            connectMotors,
            setLimits
        ], p=0, element_justification="c"),
     
        sg.Col(
        [
            dPad, 
            positions
        ], p=0, element_justification="c"),
    ],
    [otherParameters]
]

window = sg.Window('Crane Controller', layout, element_justification="c", icon=r"./icons/CraneIcon.png", use_default_focus=False)  # Build the Application Window


#-------------------------------------------------------------------- M A I N   E V E N T   L O O P --------------------------------------------------------------------
while True:
    event, values = window.read()
    
    if event == sg.WINDOW_CLOSED:              # if the user closes the program                                     
        break                                  # break the loop

#--------------------------------------------------------------------- C O N N E C T   M O T O R S ---------------------------------------------------------------------   
    if event == "-CONNECT_X-":                                 # If the user presses the button to connect the x motor
        xPort = str(values['-X_PORT-'])                        # Convert input to a string
        xPort = xPort[0:(xPort.index("-")-1)]                  # Get the directory of the port selected (remove the device name)
        
        xBaudrate = str(values['-X_BAUD-'])                    # Convert the baudrate to a string
        
        x.connectMotor(xPort, xBaudrate)                       # Connect to the specified serial port at the specified baud rate
        
        window['-CONNECT_X-'].update(button_color='green')     # and change the connect button colour to green
        
    if event == "-CONNECT_Y-":                                 # If the user presses the button to connect the x motor
        yPort = str(values['-Y_PORT-'])                        # Convert input to a string
        yPort = yPort[0:(yPort.index("-")-1)]                  # Get the directory of the port selected (remove the device name)
        
        yBaudrate = str(values['-Y_BAUD-'])                    # Convert the baudrate to a string
        
        y.connectMotor(yPort, yBaudrate)                       # Connect to the specified serial port at the specified baud rate
        
        window['-CONNECT_Y-'].update(button_color='green')     # and change the connect button colour to green
    
    
#------------------------------------------------------------------------- S E T   L I M I T S ------------------------------------------------------------------------- 
    if event == "-SET_X_LIM-":                                                  # If the user presses the set X limit button
        x.setLimits(float(values['-X_LOW_LIM-']), float(values['-X_UP_LIM-']))  # set the X axis lower and upper limits to the specified values
     
   
    if event == "-SET_Y_LIM-":                                                  # If the user presses the set Y limit button
        x.setLimits(float(values['-Y_LOW_LIM-']), float(values['-Y_UP_LIM-']))  # set the Y axis lower and upper limits to the specified values

        
         
#-------------------------------------------------------------------------- S E T   S P E E D -------------------------------------------------------------------------- 
    if event == '-SPEED-':            # If the speed slider is updated
        mmPerSec = values['-SPEED-']  # Read the mm/s value from the slider

        x.setSpeed(mmPerSec)          # Set the speed of the X axis               
        y.setSpeed(mmPerSec)          # Set the speed of the Y axis   
    

#---------------------------------------------------------------- Y   A X I S   C O M P E N S A T I O N ---------------------------------------------------------------- 
    if event == "-Y_COMP-":                   # If the Y-Axis Compensation tickbox is updated
        yCompEnabled = values["-Y_COMP-"]     # Enable or disable the Y-Axis Compensation according to the tickbox 
    

#--------------------------------------------------------------------- B U T T O N   C O N T R O L ---------------------------------------------------------------------   
    if event == "-UP-" and y.isWithinLimit("upper"):       # If the up button in the UI is pressed and the axis is within its limits
        y.stepAntiClockwise()                              # move the Y axis up 
        time.sleep(y.stepDelay)                            # delay to control the speed of the motor
        
        
    if event == "-DOWN-" and y.isWithinLimit("lower"):     # If the down button in the UI is pressed and the axis is within its limits
        y.stepClockwise()                                  # move the Y axis down
        time.sleep(y.stepDelay)                            # delay to control the speed of the motor
        
        
    if event == "-RIGHT-" and x.isWithinLimit("upper"):    # If the right button in the UI is pressed and the axis is within its limits
        x.stepAntiClockwise()                              # move the X axis right
        
        if yCompEnabled:                                   # if Y axis compensation is enabled
            if random.random() < yCompStepsPerXStep:       # for every (~0.55) X steps 
                y.adjustClockwise()                        # Move the Y axis 1 step down (to keep the hook at the same level)                               
        
        time.sleep(x.stepDelay)                            # delay to control the speed of the motor
        
        
    if event == "-LEFT-" and x.isWithinLimit("lower"):     # If the left button in the UI is pressed and the axis is within its limits
        x.stepClockwise()                                  # move the X axis left
        
        if yCompEnabled:                                   # if Y axis compensation is enabled
            if random.random() < yCompStepsPerXStep:       # for every (~0.55) X steps 
                y.adjustAntiClockwise()                    # Move the Y axis 1 step up (to keep the hook at the same level)  
                
        time.sleep(x.stepDelay)                            # delay to control the speed of the motor
    
    
    window['-X-'].update(round(x.position, 2))             # Update the X position value displayed in the UI
    window['-Y-'].update(round(y.position, 2))             # Update the Y position value displayed in the UI

    '''
#------------------------------------------------------------------- K E Y B O A R D   C O N T R O L -------------------------------------------------------------------   
    if keyboard.is_pressed('up') and y.isWithinLimits():    # If the up arrow key on the keyboard is pressed and the axis is within its limits
        y.stepAntiClockwise()                               # move the Y axis up 
        time.sleep(y.stepDelay)                             # delay to control the speed of the motor
  
        
    if keyboard.is_pressed('down') and y.isWithinLimits():  # If the down arrow key on the keyboard is pressed and the axis is within its limits
        y.stepClockwise()                                   # move the Y axis down
        time.sleep(y.stepDelay)                             # delay to control the speed of the motor
 
        
    if keyboard.is_pressed('right') and x.isWithinLimits(): # If the right arrow key on the keyboard is pressed and the axis is within its limits
        x.stepAntiClockwise()                               # move the X axis right
        
        if yCompEnabled:                                    # if Y axis compensation is enabled
            if random.random() < yCompStepsPerXStep:        # for every (~0.55) X steps 
                y.adjustClockwise()                         # Move the Y axis 1 step down (to keep the hook at the same level)                               
        
        time.sleep(x.stepDelay)                             # delay to control the speed of the motor
  
        
    if keyboard.is_pressed('left') and x.isWithinLimits():  # If the left arrow key on the keyboard is pressed and the axis is within its limits
        x.stepClockwise()                                   # move the X axis left
        
        if yCompEnabled:                                    # if Y axis compensation is enabled
            if random.random() < 0.550717266:               # for every (~0.55) X steps 
                y.adjustAntiClockwise()                     # Move the Y axis 1 step up (to keep the hook at the same level)  
                
        time.sleep(x.stepDelay)                             # delay to control the speed of the motor
  
    
    window['-X-'].update(round(x.position, 2))              # Update the X position value displayed in the UI
    window['-Y-'].update(round(y.position, 2))              # Update the Y position value displayed in the UI

    '''
#------------------------------------------------------------------------ S E T   O R I G I N S ------------------------------------------------------------------------      
    if event == "-SET_X_ORIG-":                             # If the user presses the set X origin button
        x.setOrigin()                                       # Set the X axis origin to 0
        window['-X-'].update(round(x.position, 2))          # and update the X position value displayed in the UI               
              
    if event == "-SET_Y_ORIG-":                             # If the user presses the set Y origin button
        y.setOrigin()                                       # Set the Y axis origin to 0
        window['-Y-'].update(round(y.position, 2))          # and update the Y position value displayed in the UI  
        
       
#-------------------------------------------------------------------- M O V E   T O   O R I G I N S --------------------------------------------------------------------       
    if event == "-TO_X_ORIG-":                              # If the user presses the 'To X Origin' button
        while x.isWithinLimit("lower"):                     # continue until the crane has reached the left side
            x.stepClockwise()                               # move the X axis left
        
            if yCompEnabled:                                # if Y axis compensation is enabled
                if random.random() < yCompStepsPerXStep:    # for every (~0.55) X steps 
                    y.adjustAntiClockwise()                 # Move the Y axis 1 step up (to keep the hook at the same level) 
                    
            window['-X-'].update(round(x.position, 2))      # and update the X position value displayed in the UI
                    
            time.sleep(x.stepDelay)                         # delay to control the speed of the motor

         
          
    if event == "-TO_Y_ORIG-":                              # If the user presses the 'To Y Origin' button
        while y.isWithinLimit("upper"):                     # continue until the crane has reached the top
            y.stepAntiClockwise()                           # move the Y axis up 
            
            window['-Y-'].update(round(y.position, 2))      # and update the Y position value displayed in the UI
            
            time.sleep(y.stepDelay)                         # delay to control the speed of the motor
                       
   
# If the user has quit the program, the main loop breaks and this code will execute    
    
window.close()         # close the window

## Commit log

2023-09-25 V0.1.0 Started Documenting Project
    [Urumbu_Crane_3D_Printed_Parts_V1.1.stl, Urumbu_Crane_MDF_Parts.f3z, Urumbu_Crane_MDF_Parts_2.f3z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]
2023-09-26 V0.2.0 Documented Design Features and Assembly
